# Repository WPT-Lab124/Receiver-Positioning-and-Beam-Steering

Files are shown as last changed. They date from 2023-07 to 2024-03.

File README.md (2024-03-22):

# Receiver Positioning and Beam Steering

NEWS: 🔥Our paper is accepted by iScience!🔥

[Design principles and implementation of receiver positioning and beam steering for laser power transfer systems](https://www.cell.com/iscience/fulltext/S2589-0042(23)02259-9)

Minshen Lin, Wenxing Zhong





This project is the implementation of our proposed scheme of receiver positioning and beam steering for laser power transfer systems. With the hardware design models and the source code, you can replicate the findings in our paper and explore new ideas and schemes based on the current design. If you require any further information or if we can be of any assistance, feel free to contact us by creating an [issue](https://github.com/WPT-Lab124/Receiver-Positioning-and-Beam-Steering/issues) or sending us emails.

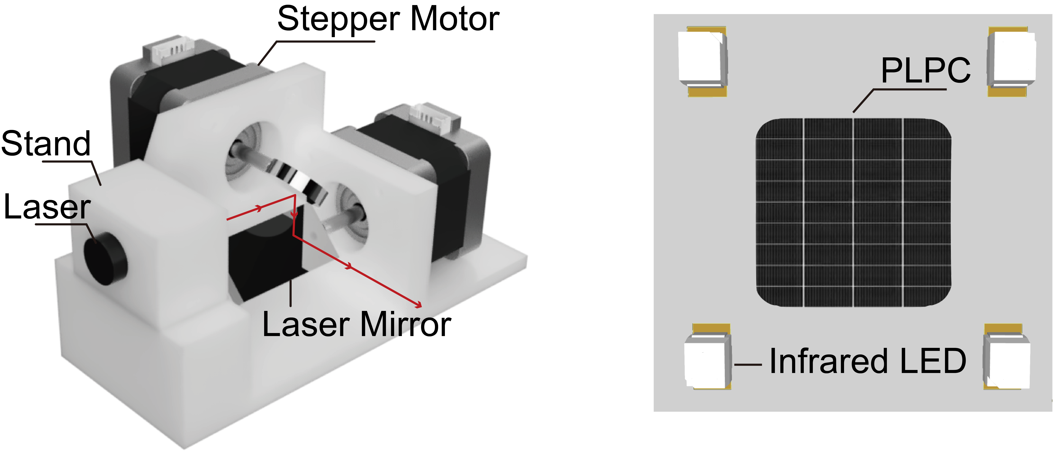
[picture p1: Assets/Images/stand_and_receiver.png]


This project includes:
- source code (in Python) that implements the functionalities and the experimental protocols
- 3D-printing models (STL files) for the mechanical design
- PCB design for the receiver
- experimental results in video form
- bill of materials

## Project structure
```
├── Code
│   ├── main.py                       <- main file implementing the control logic described in the paper
│   ├── protocol_1.py                 <- file for experimental protocol 1
|   ├── protocol_2.py                 <- file for experimental protocol 2
│   └── Utils
│   │   ├── PID.py                    <- PID controller class
│   │   ├── ReceivedPoints.py         <- class for discerning the receiver from the captured 5 points
│   │   ├── StepperMotor.py           <- motor controller class
│   │   └── tracker.py                <- tracker class
├── Hardware                          <- hardware design models
│   ├── 3D-Printing Models
│   └── Printed Circuit Board
├── Assets                            <- images and experimental videos for the protocols
│   ├── Images
│   └── Videos
├── LICENSE.md 
└── README.md
```

## Preparation
- To get started, you need to have two stepper motors, two motor controllers, Raspberry Pi 4B with Camera module v2 (or other computers and cameras, but the code needs modification), an infrared filter, an infrared laser (e.g., 100 mW, 808nm), and two laser mirrors.
- Manufacture the 3D-printing models and the PCB, and assemble everything.
- Set up the Python environment on Raspberry Pi. See [Ref](https://www.youtube.com/watch?v=QzVYnG-WaM4&t=2s).
- Download the code on your Raspberry Pi.
- Test the system performance with `main.py`, `protocol_1.py`, or `protocol_2.py`.

A photo of the implementation is shown in the following image. The photovoltaic (PV) cell is manufactured by our collaborators, but you can use the receiver without PV cells because it has negligible influence on the intensity of the laser spot beamed at the receiver.

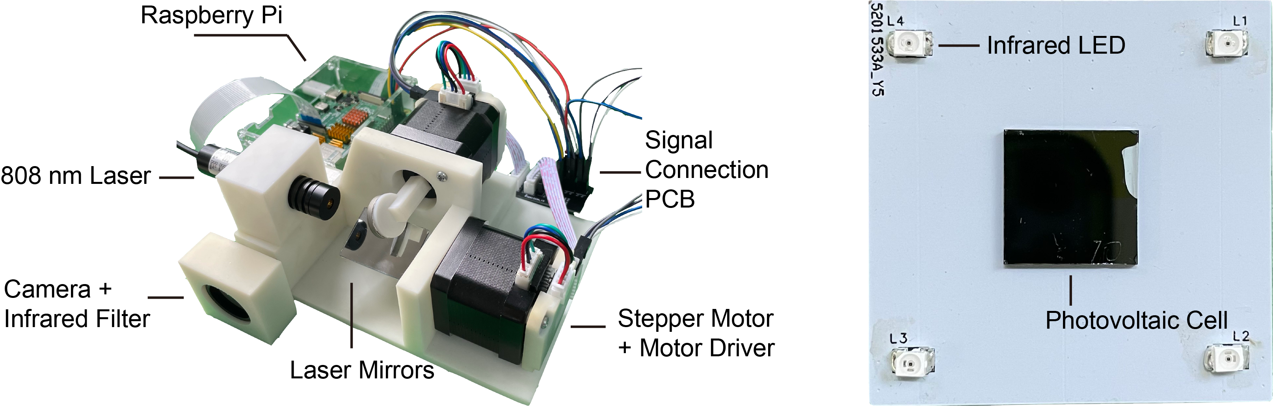
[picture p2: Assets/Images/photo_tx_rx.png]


## Experimental Videos
### Protocol 1
***With 16 microstepping***

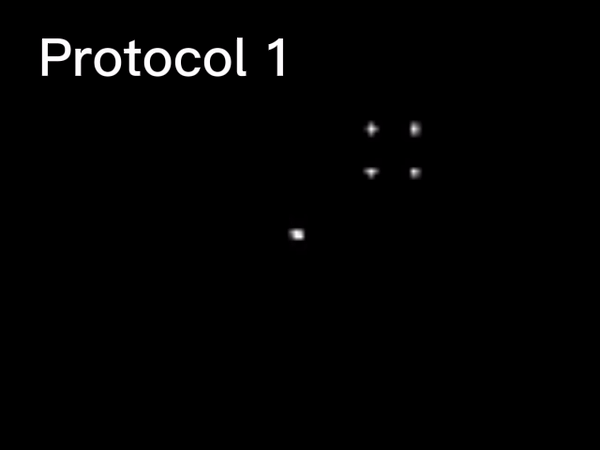
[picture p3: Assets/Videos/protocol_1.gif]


Parameters: the distance between the transmitter and the receiver is 2 m; the initial distance between the receiver and the laser spot is 10 cm.

***With 256 microstepping***

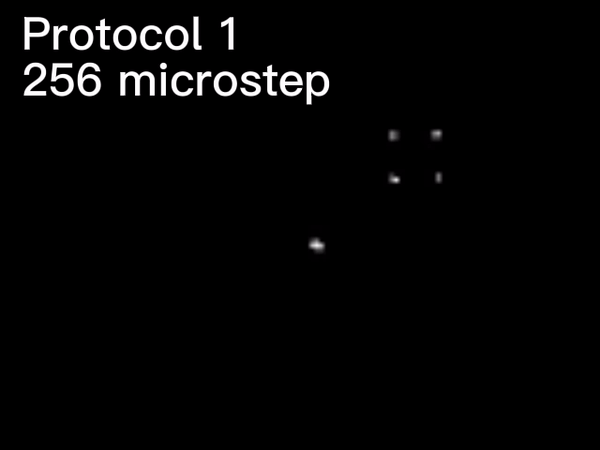
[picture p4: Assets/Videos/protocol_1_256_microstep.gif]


### Protocol 2
***With 1 cm/s receiver speed***

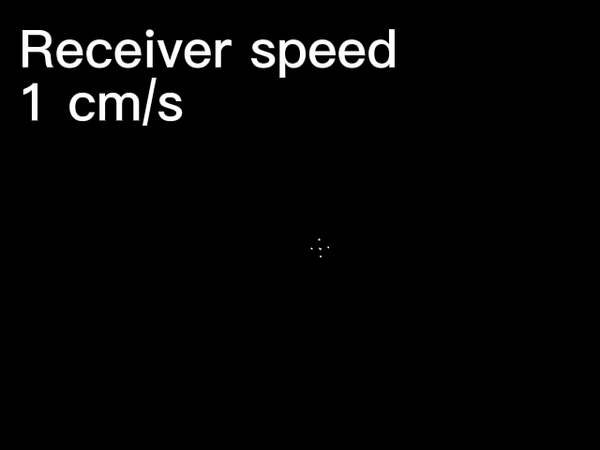
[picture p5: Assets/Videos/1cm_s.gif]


***With 5 cm/s receiver speed***

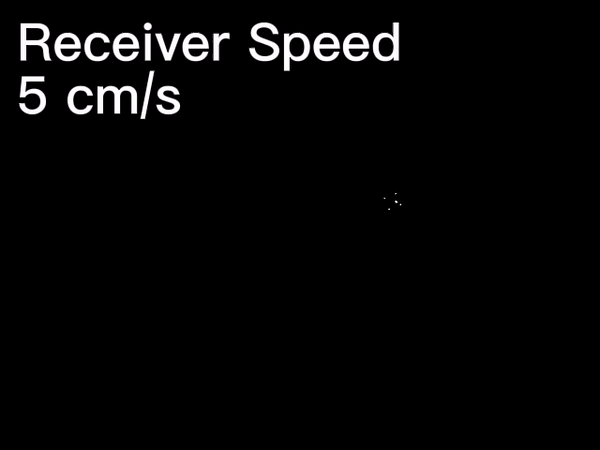
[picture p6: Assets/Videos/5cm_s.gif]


***With 10 cm/s receiver speed***

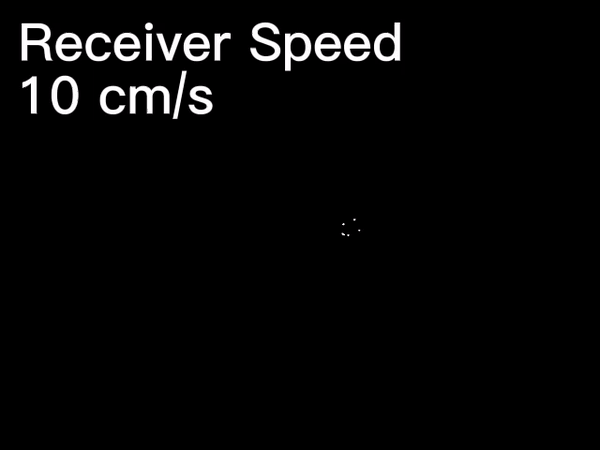
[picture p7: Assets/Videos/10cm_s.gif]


## Bill of Materials
For researchers in China, you can purchase the components in the following links:
- [Stepper Motor](https://item.taobao.com/item.htm?spm=a1z09.2.0.0.52632e8d1TXj6z&id=600124844336&_u=528s2ekd5bd1)
- [Motor Controller](https://item.taobao.com/item.htm?spm=a1z09.2.0.0.52632e8d1TXj6z&id=673302946671&_u=528s2ekd75e7)
- [Raspberry Pi 4B](https://item.taobao.com/item.htm?spm=a1z09.2.0.0.52632e8dekqXXo&id=596761703325&_u=528s2ekdece8)
- [Raspberry Pi Camera Module v2](https://item.taobao.com/item.htm?spm=a1z09.2.0.0.52632e8dekqXXo&id=531388836999&_u=528s2ekdae12)
- [Infrared Filter](https://item.taobao.com/item.htm?spm=a1z09.2.0.0.52632e8d39Q22d&id=41482304810&_u=528s2ekdcfbc)
- [Infrared Laser](https://item.taobao.com/item.htm?spm=a1z09.2.0.0.52632e8d1TXj6z&id=597192207671&_u=528s2ekd5970)
- [Laser Mirror (circular)](https://item.taobao.com/item.htm?spm=a1z09.2.0.0.52632e8d1TXj6z&id=586249224446&_u=528s2ekddfc6)
- [Laser Mirror (rectangular)](https://item.taobao.com/item.htm?spm=a1z09.2.0.0.52632e8d1TXj6z&id=577756381316&_u=528s2ekdd99e)
- [PCB Manufacturing](https://www.jlc.com/)
- [3D Printing](https://www.sanweihou.com/)

For researchers outside China, you can purchase similar components on other platforms.

If we can be of any assistance or if you require any further information, feel free to contact us.

## Citation
If you find this work useful in your research, please cite:
```
@article{lin2023design,
  title={Design principles and implementation of receiver positioning and beam steering for laser power transfer systems},
  author={Lin, Minshen and Zhong, Wenxing},
  journal={Iscience},
  volume={26},
  number={11},
  year={2023},
  publisher={Elsevier}
}
```

## Other Info.
Author: Minshen Lin and Wenxing Zhong

Email: linminshen@zju.edu.cn, wxzhong@zju.edu.cn

Institution: Zhejiang University

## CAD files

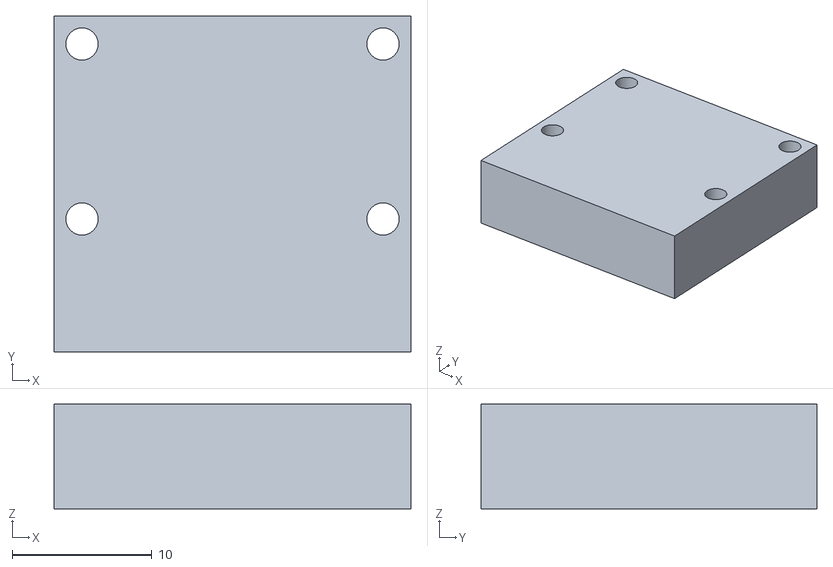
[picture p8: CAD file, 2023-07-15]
Hardware/3D-Printing Models/camera_case_part2.stl
25.5 x 24.0 x 7.50

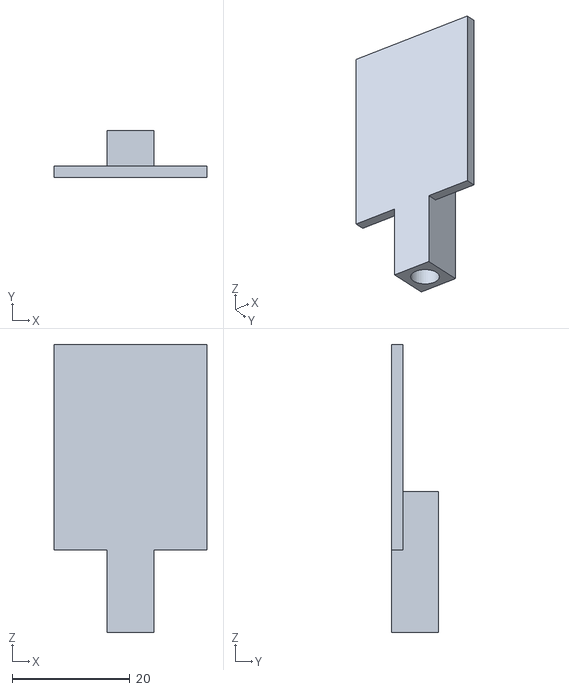
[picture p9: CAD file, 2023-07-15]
Hardware/3D-Printing Models/rectengular_mirror.stl
26.0 x 8.00 x 49.0

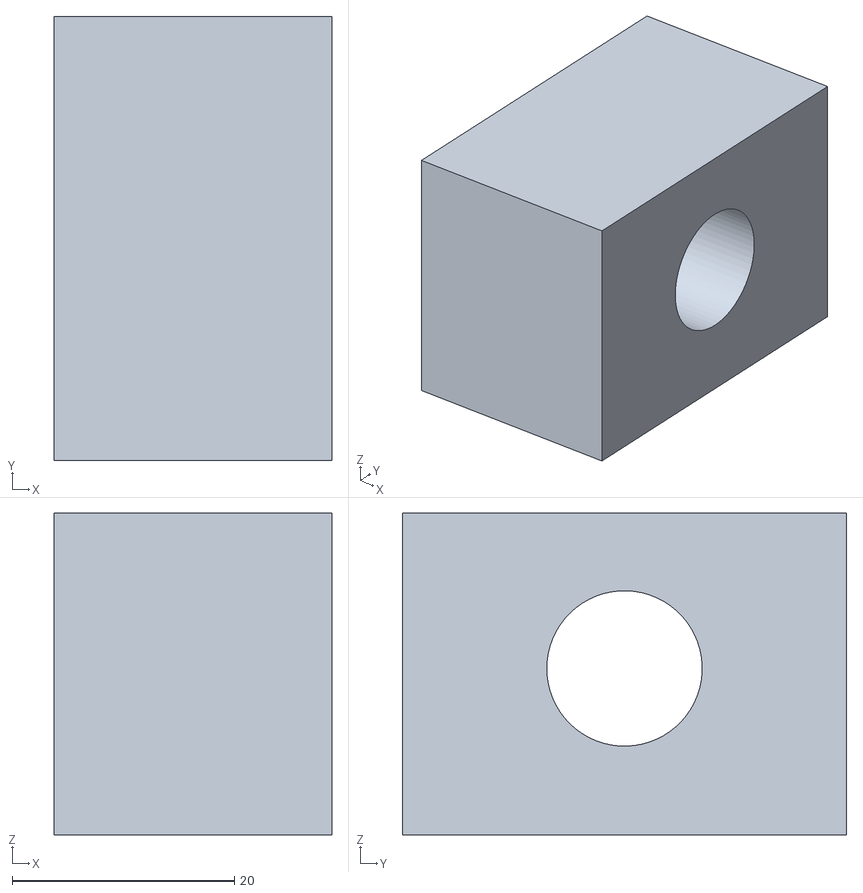
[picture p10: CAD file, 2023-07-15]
Hardware/3D-Printing Models/laser_stand.stl
25.0 x 40.0 x 29.0

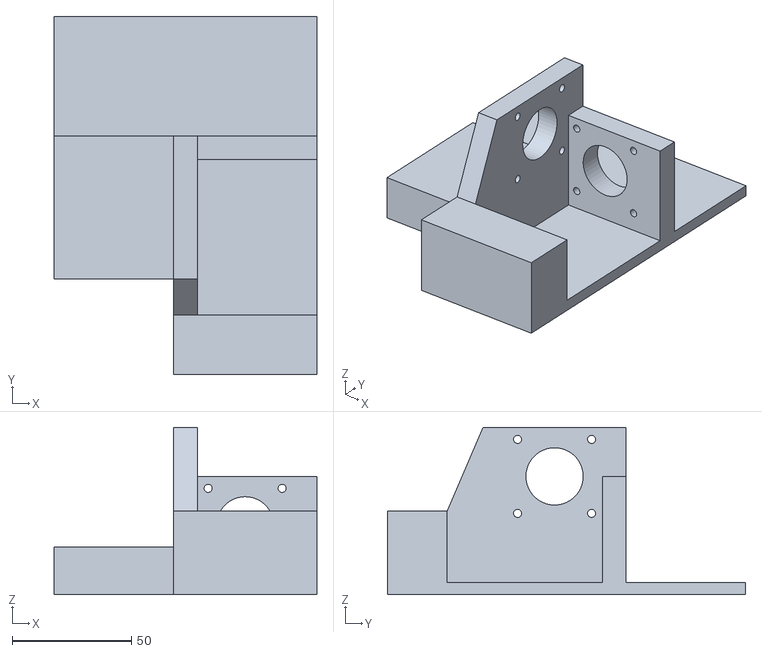
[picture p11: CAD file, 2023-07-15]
Hardware/3D-Printing Models/stand.stl
110.0 x 150.0 x 70.0

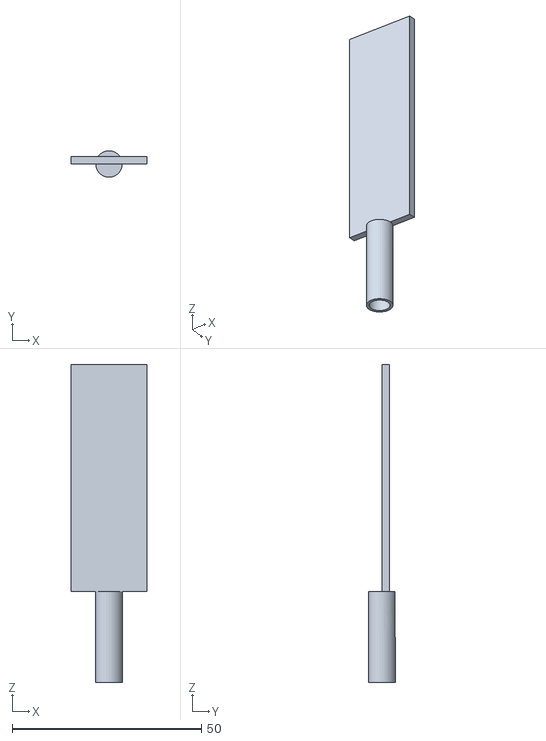
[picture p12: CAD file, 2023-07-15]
Hardware/3D-Printing Models/rectengular_mirror_large.stl
20.0 x 7.00 x 84.0

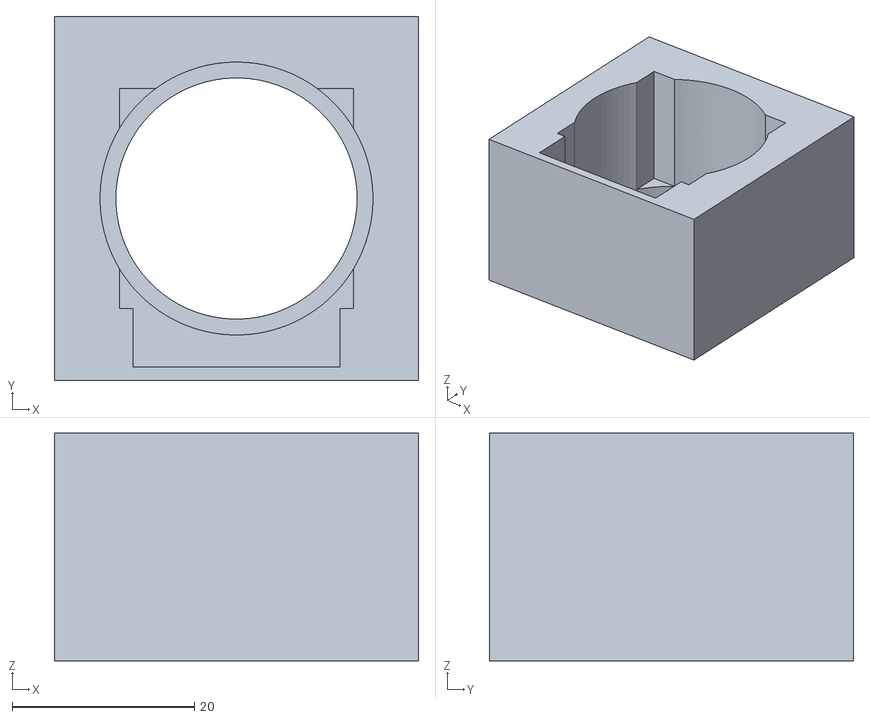
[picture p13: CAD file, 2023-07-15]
Hardware/3D-Printing Models/camera_case_part1.stl
40.0 x 40.0 x 25.0

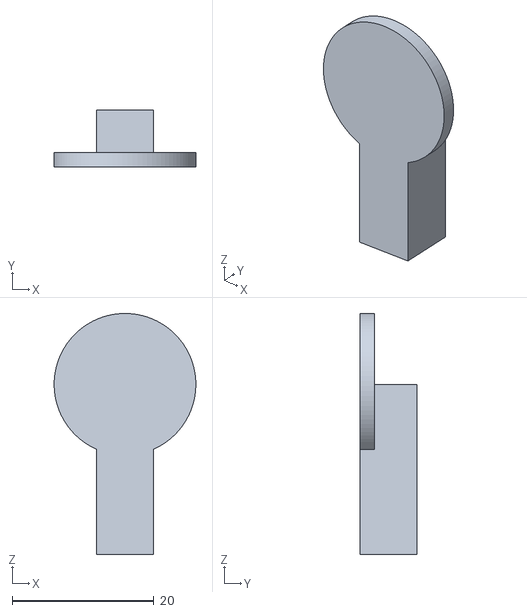
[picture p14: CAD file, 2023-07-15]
Hardware/3D-Printing Models/circular_mirror.stl
20.0 x 8.00 x 34.0

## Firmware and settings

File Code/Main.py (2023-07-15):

#!/usr/bin/env python3
# -*- coding: utf-8 -*-
"""
The program that implements receiver localization and beam steering.

@ Author: Minshen Lin
@ Institute: Zhejiang University

@ LICENSE
This program is free software: you can redistribute it and/or modify
it under the terms of the GNU General Public License as published
by the Free Software Foundation, either version 3 of the License, or
(at your option) any later version.
"""

import cv2
import numpy as np
import subprocess as sp
import time
import datetime

# initialization stage
# initialize serial port with a default baudrate of 115200
import serial
serial_port = serial.Serial("/dev/serial0", 115200)

# initialize stepper motor controllers
from Utils.StepperMotor import Motor
motor_horizontal = Motor(serial_port, b'\x01')
motor_horizontal.set_angle_limits(-10, 10)
motor_vertical = Motor(serial_port, b'\x02')
motor_vertical.set_angle_limits(-10, 10)

# initialize PID controllers
from Utils.PID import PID
kp = -0.01; ki = -0.1; kd = 0
pid_vertical = PID(Kp = kp, Ki = ki, Kd = kd, setpoint = 0, sample_time = 0.033, output_limits = (-20, 20), differential_on_measurement = True)
pid_horizontal = PID(Kp = kp, Ki = ki, Kd = kd, setpoint = 0, sample_time = 0.033, output_limits = (-20, 20), differential_on_measurement = True)

# initialize a ReceivedPoints and a tracker to manage camera-captured contours
from Utils.ReceivedPoints import ReceivedPoints
from Utils.Tracker import Tracker
received_points = ReceivedPoints()
tracker = Tracker(received_points)

# global parameters
frame_count_limit = 1000 # modify this variable to change the operation time of the system
prevNumOfContours = 0
frame_count = 0
motor_enable = False

# operation stage
frames = []
frame_count = 0

# Video capture parameters
# (1280, 960) @ 40 fps
(width, height) = (1280, 960)
bytesPerFrame = width * height
fps = 40

# "raspividyuv" is the command that provides camera frames in YUV format
#  "--output -" specifies stdout as the output
#  "--timeout 0" specifies continuous video
#  "--luma" discards chroma channels, only luminance is sent through the pipeline
# see "raspividyuv --help" for more information on the parameters
videoCmd = "raspividyuv -w " + str(width) + " -h " + str(height) + " --output - --timeout 0 --framerate " + str(fps) + " --luma --nopreview"
videoCmd = videoCmd.split() # Popen requires that each parameter is a separate string

# initialize the parallel camera process
with sp.Popen(videoCmd, stdout = sp.PIPE) as cameraProcess:
    start_time = time.time()
    
    # wait for the first frame and discard it (only done to measure time more accurately)
    rawStream = cameraProcess.stdout.read(bytesPerFrame)
    
    print("Starting test protocol.")
    tracker.reset_storage()
    
    while frame_count < frame_count_limit:
        cameraProcess.stdout.flush() # discard any frames that we were not able to process in time
        
        frame = np.frombuffer(cameraProcess.stdout.read(bytesPerFrame), dtype=np.uint8) # Parse the raw stream into a numpy array
        
        if frame.size != bytesPerFrame:
            print("Error: Camera stream closed unexpectedly")
            break
        
        frame.shape = (height, width) # set the correct dimensions for the numpy array
        frame = cv2.inRange(frame, 50, 255) # create binary image
        contours, _ = cv2.findContours(frame, cv2.RETR_EXTERNAL, cv2.CHAIN_APPROX_SIMPLE)
        
        frame_count += 1
        frames.append(frame) # store frames for future visualization
        
        # control logics
        if motor_enable == False:
            # if 5 contours are captured
            if len(contours) == 5:
                (center1, _) = cv2.minEnclosingCircle(contours[0])
                (center2, _) = cv2.minEnclosingCircle(contours[1])
                (center3, _) = cv2.minEnclosingCircle(contours[2])
                (center4, _) = cv2.minEnclosingCircle(contours[3])
                (center5, _) = cv2.minEnclosingCircle(contours[4])
                point_set = (center1, center2, center3, center4, center5)
                tracker.update(point_set) # update positions in the tracker
            
            if frame_count >= 100:
                motor_enable = True
                pid_horizontal.reset() # reset PID controllers, particularly the internal recorded time
                pid_vertical.reset()
            
            continue
       
        # if 5 contours are captured
        if len(contours) == 5:
            (center1, _) = cv2.minEnclosingCircle(contours[0])
            (center2, _) = cv2.minEnclosingCircle(contours[1])
            (center3, _) = cv2.minEnclosingCircle(contours[2])
            (center4, _) = cv2.minEnclosingCircle(contours[3])
            (center5, _) = cv2.minEnclosingCircle(contours[4])

            point_set = (center1, center2, center3, center4, center5)
            tracker.update(point_set) # update positions in the tracker
            (xSP, ySP), (xPV, yPV) = tracker.positions()
            
            # update PID setpoints and process variables
            pid_horizontal.setpoint = xSP
            xMV = pid_horizontal(xPV)
            time.sleep(0.005)
            motor_horizontal.move_to(xMV)
            
            pid_vertical.setpoint = ySP
            yMV = pid_vertical(yPV)
            time.sleep(0.005)
            motor_vertical.move_to(yMV)
            
            # record last-frame info
            prevNumOfContours = 5
            xSP_prev = xSP
            xPV_prev = xPV
            ySP_prev = ySP
            yPV_prev = yPV

        # if 4 contours are captured and 5 contours were captured in the last frame  
        if len(contours) == 4 and prevNumOfContours == 5:
            # perturb the stepper motors
            pid_horizontal.setpoint = xSP_prev
            xMV = pid_horizontal(xPV_prev)
            time.sleep(0.005)
            motor_horizontal.move_to(xMV)
            
            pid_vertical.setpoint = ySP_prev
            yMV = pid_vertical(yPV_prev)
            time.sleep(0.005)
            motor_vertical.move_to(yMV)
            
            prevNumOfContours = 4

    end_time = time.time()
    print("Done! Result: " + str(frame_count / (end_time - start_time)) + " fps")

# steer the motors to their zero positions
time.sleep(0.1)
motor_vertical.move_to_origin()
time.sleep(0.1)
motor_horizontal.move_to_origin()

serial_port.close() # close the open serial port

# display captured video
print("Display frames with OpenCV...")
for frame in frames:
    cv2.imshow("frame", frame)
    cv2.waitKey(1)
cv2.destroyAllWindows()

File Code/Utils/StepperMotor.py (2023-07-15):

#!/usr/bin/env python3
# -*- coding: utf-8 -*-
"""
StepperMotor class for the position control of stepper motors.

@ Author: Minshen Lin
@ Institute: Zhejiang University

@ LICENSE
This program is free software: you can redistribute it and/or modify
it under the terms of the GNU General Public License as published
by the Free Software Foundation, either version 3 of the License, or
(at your option) any later version.
"""

import serial
import math
import time

def _degr2rad(angle):
    """
    Convert angle from degree to radian
    """
    return angle / 360 * 2 * math.pi

def _rad2deg(angle):
    """
    Convert angle from radian to degree
    """
    return angle / 2 / math.pi * 360

class Motor:
    '''
    The motor class keeps track of the state of a stepper motor and allows the
    user to steer the motor to the specified angle.
    '''
    
    micro_step = 16 #32 #16
    deg_per_step = 1.8 / micro_step
    
    
    def __init__(self, serial_port: serial.Serial, serial_address: bytes):
        """
        Constructor for the Motor class. 
        In this class, the current num of steps with respect to origin is recorded;
        if the angle is recorded instead, truncated and accumulated errors will
        be introduced.
        @serial_port - The serial port for communication.
        @serial_address - The serial address of this motor.
        """
        self.current_step = 0
        self.serial_port = serial_port
        self.serial_address = serial_address
        self.angle_limits = (0, 360)
   
    def angle_to_step(self, angle):
        """
        Converts angle (in degree) to the number of steps required to reach
        that angle.
        """
        current_angle = self.current_angle()
        angular_diff = angle - current_angle
        return int(angular_diff / Motor.deg_per_step)

    def current_angle(self):
        """
        Computes the current angle from recorded number of steps.
        """
        return self.current_step * Motor.deg_per_step
    
    
    def move_to(self, angle):
        """
        Steer the motor to the specified 'angle'. This function is written in a
        recursive manner to reduce redundancy.
        """
        # if angle exceeds angular limits, steer the motor to the limiting angles
        if self._is_angle_exceeding_upper_bound(angle):
            self.move_to(self.angle_limits[1])
            return
        elif self._is_angle_exceeding_lower_bound(angle):
            self.move_to(self.angle_limits[0])
            return
        
        # otherwise, steer the motor to the specified angle
        num_of_steps = self.angle_to_step(angle)
        if num_of_steps == 0:
            return
        # generate a serial command for steering
        command = bytearray(self.serial_address) # motor serial address （1 byte）
        # code 0xFD for moving command （1 byte）
        command.extend(b'\xfd')
        # direction， speed， and acceleration （3 bytes）
        if num_of_steps > 0:
            command.extend(b'\x14\xff\x00')
        else:
            command.extend(b'\x04\xff\x00')
        command.extend(abs(num_of_steps).to_bytes(3, byteorder = 'big')) # num of steps （3 bytes）
        command.extend(b'\x6b') # parity check （1 byte）
        
        self.serial_port.write(command) # write the command to motor via serial port
        self.current_step += num_of_steps # record the current num of steps
    
    def move_to_origin(self):
        """
        Steers the motor to origin (0 deg).
        """
        self.move_to(0)
        
    def set_current_pos_as_origin(self):
        """
        Sets the current position as the new origin point.
        """
        command = bytearray(self.serial_address)
        command.extend(b'\x0a\x6d\x6b')
        print('set command is')
        print(command)
        self.serial_port.write(command)
        self.current_step = 0
        
    def set_origin_to_angle(self, angle):
        """
        """
        self.move_to(angle)
        time.sleep(0.01)
        self.set_current_pos_as_origin()
    
    def set_angle_limits(self, lower_bound: float, upper_bound: float):
        """
        Set angle limits that the motor can move within.
        """
        self.angle_limits = (lower_bound, upper_bound)
        
    def _is_angle_exceeding_upper_bound(self, angle):
        """
        Whether the angle exceeds the upper angle limit.
        """
        if angle > self.angle_limits[1]:
            return True
        return False
    
    def _is_angle_exceeding_lower_bound(self, angle):
        """
        Whether the angle exceeds the lower angle limit.
        """
        if angle < self.angle_limits[0]:
            return True
        return False
     

if __name__ == '__main__':
    # Testing the functionalities of this class
    
    # initialize seiral with a default baudrate of 115200
    serial_port = serial.Serial("/dev/serial0", 115200)
    motor1 = Motor(serial_port, b'\x01')
    motor1.set_angle_limits(-22.5, 22.5)
    
    # motor1.set_origin_to_angle(-2.5) # negative number moves right
    
    time.sleep(0.1)
    
    motor2 = Motor(serial_port, b'\x02')
    motor2.set_angle_limits(-22.5, 22.5)
    

    motor2.set_origin_to_angle(-2.5) # negative number moves downwards
        
    serial_port.close()

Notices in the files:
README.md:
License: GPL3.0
